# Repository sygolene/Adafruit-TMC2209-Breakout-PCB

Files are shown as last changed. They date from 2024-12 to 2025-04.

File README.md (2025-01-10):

## Adafruit TMC2209 Stepper Motor Driver Breakout Board PCB

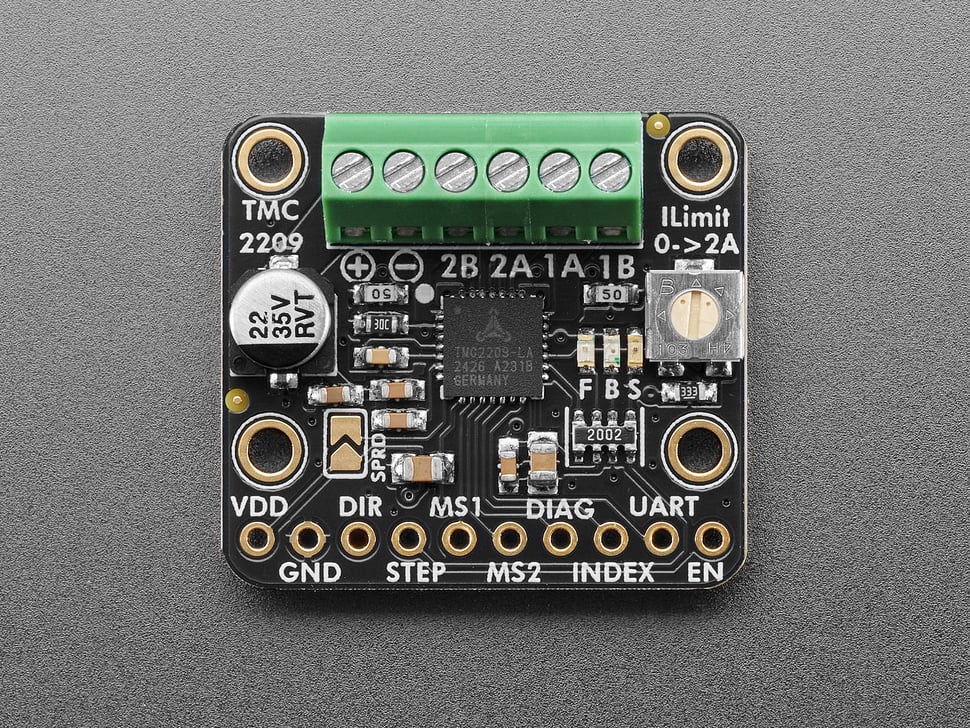
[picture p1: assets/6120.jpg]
<a href="http://www.adafruit.com/products/6121"><br/>
Click here to purchase one from the Adafruit shop</a>

PCB files for the Adafruit TMC2209 Stepper Motor Driver Breakout Board. 

Format is EagleCAD schematic and board layout
* https://www.adafruit.com/product/6121

### Description

Stepper motors are used for CNC machines, 3D printers, and whenever else one needs precise, powerful motion. But to get good behavior from steppers you need a motor driver chip that can provide high bursts of current, and for smooth motion, be able to PWM that current for microstepping support. You can DIY this with a lot of timers, a microcontroller and an  H-Bridge chip - or you could take the easy way out and use an Adafruit TMC2209 Stepper Motor Driver Breakout Board which makes controlling stepper motors easy-breezy and super-silent. 

All you need is two output pins, no timers, PWM or real-time microcontroller. Set the DIRection pin high or low to set the spin orientation. Then toggle the STEP pin to take one microstep at a time. You can set whether you want to go faster with 1/8 microsteps, or increase the precision to 1/16, 1/32 or 1/64 microsteps per STEP toggle. If you want more control, say to single-step or up to 1/256 microsteps, you can do so via the UART interface (more on that later). By default the driver is set to 1/8 microstep mode, you can change it by tying the MS1/MS2 pins high, either with jumpers or with 2 more output pins. The step/microstep mode can even be adjusted on the fly! LEDs on the DIR and STEP pins let you get visual feedback of your motor signal.

The Trinamic drivers are often known as "silent" or "stealth" chips - compared to the A4988 they are unbelievably quiet, you can barely tell they are running thanks to the microstepping techniques used. This reduces noise and wear, to make users happy. There's also a lot of niceties like index output which will pulse when the microstepping counter cycles back to 'zero', and a diagnostic output to quickly alert the microcontroller of a big error like short or open circuits. It can also do 'sensor-less stop detection' with a feature called StallGuard - but for that you will need to use the UART interface.

The UART interface is a single-pin serial port with auto-baud detection that allows more precise communication, diagnostics and control. You can do things like set microsteps from 1 to 256, or set the speed with a single command. You can also configure settings like current limiting, over-heat temperature limit, PWM frequency, etc. You'll need a microcontroller library to use UART and it's an 'extra' - not essential for basic motion control! 

The Trinamic TMC2209 is a popular driver chip, with small breakout boards used in many 3D printers. Those breakouts are great for plugging into motherboards, but are a little tough to use for prototyping. Our version comes with terminal blocks for the motor power and stepper wires, plus nicely labeled pins for control and mounting holes.

We fabricated the board with 2 oz copper to give it a hand with the 2A-max current that this driver can handle. To use the current limiting capability, twist the onboard potentiometer: when all the way to the right we can get to up to 2A max. Note that the higher the currents will heat up both the motor driver and stepper so you may need to add heatsinking to the chip. We don't include a heatsink but you can get a tall ~80ºC/W or short ~90ºC/W heatsink to attach on top.

Features:

* Trinamic TMC2209 silent "Stealth Chopper" DMOS microstepping driver with translator and overcurrent protection
* Motor voltage from 5V to 29VDC
* Vdd/Logic voltage from 3V to 5V, use with anything from an Arduino-compatible or ESP32 to Raspberry Pi other Single Board Computer
* Terminal screw block connections for easy VMotor power and 4-wire bi-polar stepper motor connection with 26-20AWG slots, 2.54mm / 0.1" spacing
* Control steppers using only two pins: DIRection and STEP
* Defaults to 1/8 microstep mode, change by pulling MS1/MS2 high (see TMC2209 datasheet for pin configuration) or via UART
* Red and Green LEDs on DIR signal to let you know forward or backward motion
* Yellow LED on STEP to let you know that motor driver is being moved
* Enable control line for low power / deactivation
* Index output will toggle when passing through the 'zero point' of the microsteps
* Diagnostic output will trigger on errors like shorted output or with "stall detection" (which requires UART configuration)
* Potentiometer to set current limiting, up to 2A
* 22uF 35V electrolytic capacitor on motor power
* 2 Oz copper for better current carrying and heatsinking
* Four mounting holes

Comes as one assembled and tested breakout plus a small strip of header. You'll need to do some light soldering to attach the header onto the breakout PCB. Microcontroller, motors, and power supply not included. You will need some sort of driver board that will toggle the DIR/STEP pins for you.

### License

Adafruit invests time and resources providing this open source design, please support Adafruit and open-source hardware by purchasing products from [Adafruit](https://www.adafruit.com)!

Designed by Limor Fried/Ladyada for Adafruit Industries.

Creative Commons Attribution/Share-Alike, all text above must be included in any redistribution. 
See license.txt for additional details.

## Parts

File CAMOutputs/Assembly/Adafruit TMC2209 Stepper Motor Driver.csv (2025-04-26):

Qty | Value | Device | Package | Parts | Description | BOM | POPULARITY | ROT | SPICEMODEL | SPICEPREFIXL
1 |  | HEADER-1X1070MIL | 1X10_ROUND70 | JP4 | PIN HEADER
1 |  | SOLDERJUMPER | SOLDERJUMPER_ARROW_NOPASTE | SJ1 | SMD Solder JUMPER | EXCLUDE
2 | 0.05Ω/0.25W | RESISTOR_0603_NOOUT | 0603-NO | R1, R2 | Resistors
4 | 0.22uF/50V | CAP_CERAMIC0603_NO | 0603-NO | C3, C5, C7, C8 | Ceramic Capacitors
1 | 10K | R-TRIMM3314J | RTRIM3314J | VR1 | Trimm resistor |  | 0 |  | X | POT
2 | 10uF | CAP_CERAMIC0805-NOOUTLINE | 0805-NO | C2, C6 | Ceramic Capacitors
1 | 20K | RESISTOR_0603_NOOUT | 0603-NO | R3 | Resistors
1 | 20K Pack | RESISTOR_4PACK | RESPACK_4X0603 | R5 | Resistor Packs (4 resistors)
1 | 22nF/50V | CAP_CERAMIC0603_NO | 0603-NO | C1 | Ceramic Capacitors
1 | 22uF/50V | CAP_ELECTROLYTICPANASONIC_C | PANASONIC_C | C4 | Electrolytic Capacitors
1 | 33K | RESISTOR_0603_NOOUT | 0603-NO | R4 | Resistors
1 | 6-pin 2.54 Terminal | HEADER-1X6_2.54MMTERM | 1X06_2.54MMTERMINAL | JP1 | PIN HEADER
2 | FIDUCIAL_0.5MM | FIDUCIAL_0.5MM | FIDUCIAL_0.5MM | U$10, U$11 | Fiducial Alignment Points
1 | GREEN | LED0603_NOOUTLINE | CHIPLED_0603_NOOUTLINE | D3 | LED |  |  | 270
4 | MOUNTINGHOLE2.0 | MOUNTINGHOLE2.0 | MOUNTINGHOLE_2.0_PLATED | U$18, U$22, U$26, U$27 | Mounting Hole | EXCLUDE
1 | RED | LED0603_NOOUTLINE | CHIPLED_0603_NOOUTLINE | D1 | LED |  |  | 270
1 | TMC2209_QFN | TMC2209_QFN | QFN28_5MM_MICROCHIP | X1
1 | YELLOW | LED0603_NOOUTLINE | CHIPLED_0603_NOOUTLINE | D2 | LED |  |  | 270

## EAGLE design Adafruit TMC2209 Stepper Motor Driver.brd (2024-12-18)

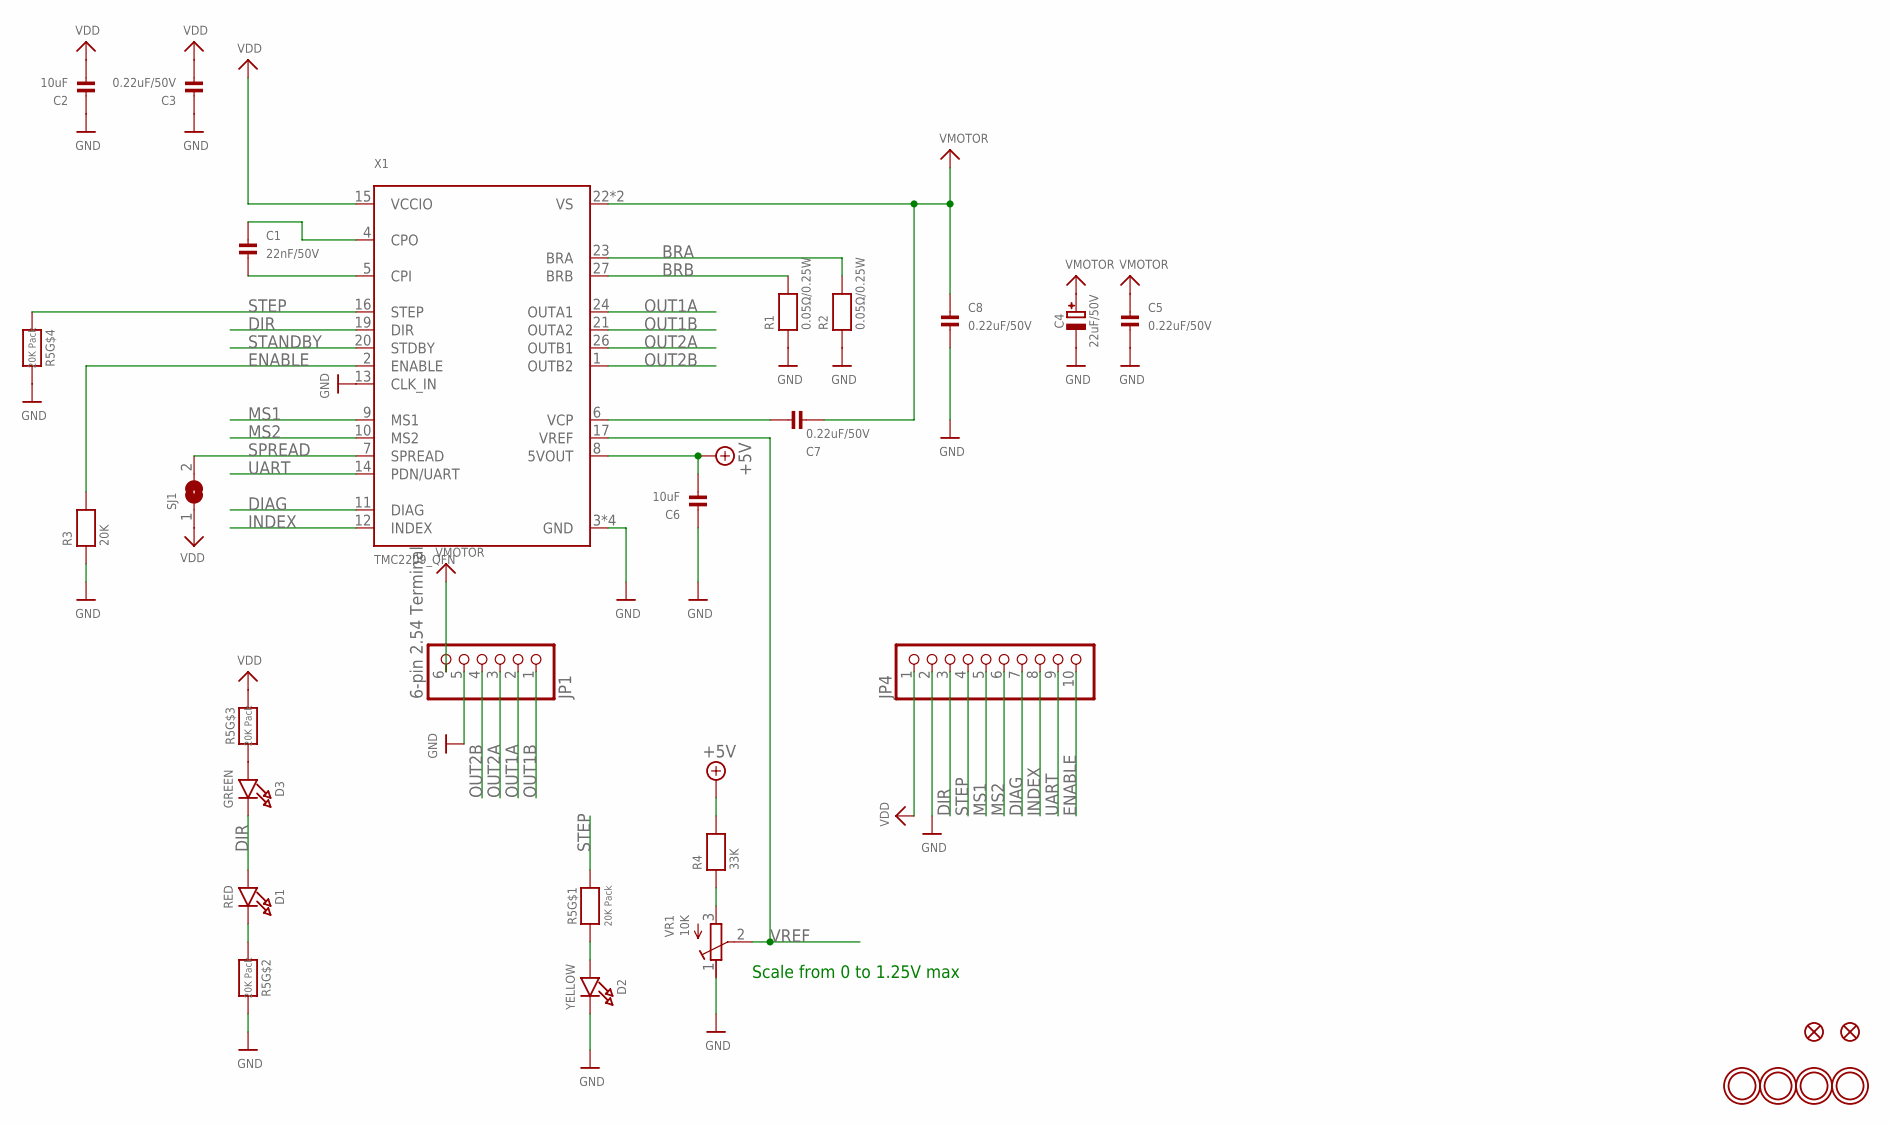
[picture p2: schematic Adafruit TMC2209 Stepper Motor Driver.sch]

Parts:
C1: 22nF/50V; 0603-NO
C2, C6: 10uF; 0805-NO
C3, C5, C7, C8: 0.22uF/50V; 0603-NO
C4: 22uF/50V; PANASONIC_C
D1: RED; CHIPLED_0603_NOOUTLINE
D2: YELLOW; CHIPLED_0603_NOOUTLINE
D3: GREEN; CHIPLED_0603_NOOUTLINE
JP1: 6-pin 2.54 Terminal; 1X06_2.54MMTERMINAL
JP4: HEADER-1X1070MIL; 1X10_ROUND70
R1, R2: 0.05Ω/0.25W; 0603-NO
R3: 20K; 0603-NO
R4: 33K; 0603-NO
R5: 20K Pack; RESPACK_4X0603
SJ1: SOLDERJUMPER; SOLDERJUMPER_ARROW_NOPASTE
U$10, U$11: FIDUCIAL_0.5MM
U$18, U$22, U$26, U$27: MOUNTINGHOLE2.0; MOUNTINGHOLE_2.0_PLATED
VR1: 10K; RTRIM3314J
X1: TMC2209_QFN; QFN28_5MM_MICROCHIP

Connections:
+5V: C6.2, R4.2, X1.8 (5VOUT)
BRA: R2.2, X1.23 (BRA)
BRB: R1.2, X1.27 (BRB)
DIAG: JP4.7, X1.11 (DIAG)
DIR: D1.A, D3.C, JP4.3, X1.19 (DIR)
ENABLE: JP4.10, R3.2, X1.2 (ENABLE)
GND: C2.1, C3.1, C4.-, C5.2, C6.1, C8.2, D2.C, JP1.5, JP4.2, R1.1, R2.1, R3.1, R5.5 (2), R5.7 (2), VR1.1 (E), X1.3 (GND), X1.13 (CLK_IN), X1.18 (GND), X1.25 (GND), X1.THERMAL (GND)
INDEX: JP4.8, X1.12 (INDEX)
MS1: JP4.5, X1.9 (MS1)
MS2: JP4.6, X1.10 (MS2)
unnamed: D2.A, R5.1
unnamed: C1.1, X1.4 (CPO)
unnamed: C1.2, X1.5 (CPI)
unnamed: R4.1, VR1.3 (A)
unnamed: C7.1, X1.6 (VCP)
unnamed: D1.C, R5.2 (1)
unnamed: D3.A, R5.3 (1)
OUT1A: JP1.2, X1.24 (OUTA1)
OUT1B: JP1.1, X1.21 (OUTA2)
OUT2A: JP1.3, X1.26 (OUTB1)
OUT2B: JP1.4, X1.1 (OUTB2)
SPREAD: SJ1.2, X1.7 (SPREAD)
STANDBY: X1.20 (STDBY)
STEP: JP4.4, R5.4 (1), R5.8 (2), X1.16 (STEP)
UART: JP4.9, X1.14 (PDN/UART)
VDD: C2.2, C3.2, JP4.1, R5.6 (2), SJ1.1, X1.15 (VCCIO)
VMOTOR: C4.+, C5.1, C7.2, C8.1, JP1.6, X1.22 (VS), X1.28 (VS)
VREF: VR1.2 (S), X1.17 (VREF)

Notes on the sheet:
Scale from 0 to 1.25V max

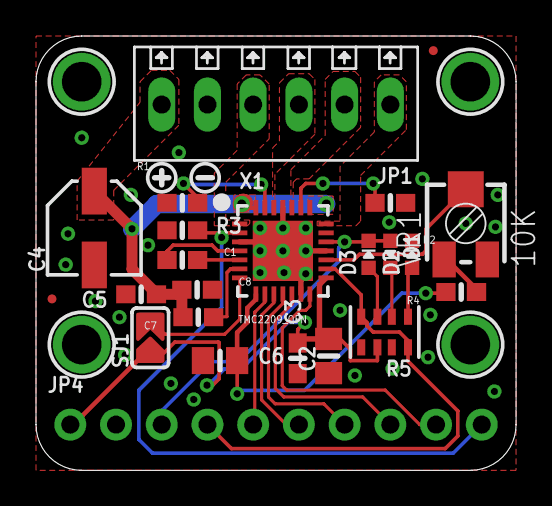
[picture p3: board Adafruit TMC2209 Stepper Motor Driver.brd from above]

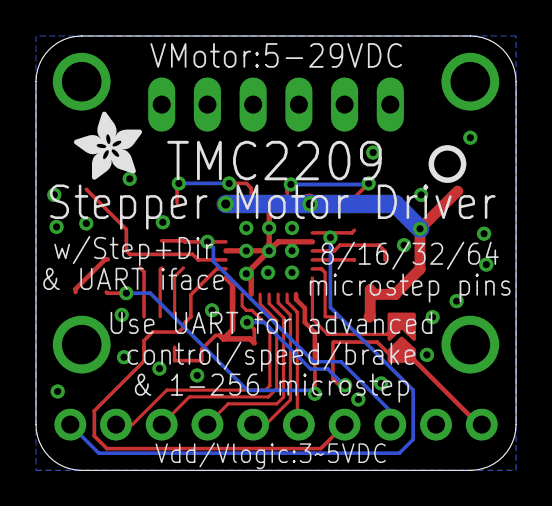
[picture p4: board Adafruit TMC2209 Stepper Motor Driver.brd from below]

Board: 2 copper layers, 26.7 x 24.1 mm, 52 parts (2 on the bottom side), 27 nets.

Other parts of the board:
PLABEL0: PLABEL0
PLABEL1: PLABEL1
PLABEL2: PLABEL2
PLABEL3: PLABEL3
PLABEL4: PLABEL4
PLABEL5: PLABEL5
PLABEL6: PLABEL6
PLABEL7: PLABEL7
PLABEL8: PLABEL8
PLABEL9: PLABEL9
PLABEL10: PLABEL10
PLABEL11: PLABEL11
PLABEL12: PLABEL12
PLABEL13: PLABEL13
PLABEL14: PLABEL14
PLABEL15: PLABEL15
PLABEL16: PLABEL16
PLABEL17: PLABEL17
PLABEL18: PLABEL18
PLABEL19: PLABEL19
PLABEL20: PLABEL20
U$7: SYMBOL_PLUS
U$8: SYMBOL_MINUS
U$12: PCBFEAT-REV-040
U$24: ADAFRUIT_3.5MM

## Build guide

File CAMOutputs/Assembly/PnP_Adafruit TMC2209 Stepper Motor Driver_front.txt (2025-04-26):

C1	8.13	11.68	0.00	22nF/50V	0603-NO
C2	16.26	6.35	90.00	10uF	0805-NO
C3	14.54	6.22	90.00	0.22uF/50V	0603-NO
C4	3.24	13.46	90.00	22uF/50V	PANASONIC_C
C5	5.84	9.78	180.00	0.22uF/50V	0603-NO
C6	10.22	6.10	0.00	10uF	0805-NO
C7	9.02	8.51	180.00	0.22uF/50V	0603-NO
C8	8.95	10.03	0.00	0.22uF/50V	0603-NO
D1	19.69	12.00	180.00	RED	CHIPLED_0603_NOOUTLINE
D2	20.89	12.00	0.00	YELLOW	CHIPLED_0603_NOOUTLINE
D3	18.48	12.00	0.00	GREEN	CHIPLED_0603_NOOUTLINE
R1	8.13	14.86	0.00	0.05Ω/0.25W	0603-NO
R2	19.69	14.86	180.00	0.05Ω/0.25W	0603-NO
R3	8.13	13.34	0.00	20K	0603-NO
R4	23.62	9.91	180.00	33K	0603-NO
R5	19.37	7.68	180.00	20K Pack	RESPACK_4X0603
SJ1	6.35	7.37	90.00		SOLDERJUMPER_ARROW_NOPASTE
U$10	22.07	23.32	0.00	FIDUCIAL_0.5MM	FIDUCIAL_0.5MM
U$11	0.89	9.53	0.00	FIDUCIAL_0.5MM	FIDUCIAL_0.5MM
VR1	23.88	13.67	0.00	10K	RTRIM3314J
X1	13.72	12.19	0.00	TMC2209_QFN	QFN28_5MM_MICROCHIP
